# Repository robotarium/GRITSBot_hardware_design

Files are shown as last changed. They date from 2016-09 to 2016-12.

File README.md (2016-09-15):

- [Overview](#overview)
- [Getting Started](#getting-started)
- [Hardware Specifications](#hardware-specifications)
- [Hardware Assembly](#hardware-assembly)

# Overview
This repository contains the GRITSBot's circuit board designs, bill of materials, hardware specifications, and 3D design files. This README file is meant to provide more detailed hardware specifications and a brief tutorial outlining how to get started with the hardware. Specifically, it explains how to program both the motor and the main board.

# Getting Started
The newest version of the GRITSBot features two microcontrollers - an Atmega168/328 (8MHz, 16/32 KB flash, 2 KB RAM) on the motor board and the ESP8266 (80/160 MHz, ~80kB DRAM (Data RAM), ~35kB IRAM (Instruction RAM)) on the main board. Both boards can be programmed through the Arduino IDE but require different toolchains (avr-gcc and Xtensa). Both boards have broken out pins to connect the programmer to. The motor board relies on SPI communication for programming, while the main board's ESP8266 chip has a built-in serial bootloader. Therefore the main board requires only a USB-to-TTL converter to program instead of a programmer for the motor board. Note that for programming, the robot has to be disassembled, i.e. the two boards have to be taken apart (the battery does not have to be disconnected, but it's advisable that the robot's power switch is in the OFF position).

## Motor board programming
The GRITSBot's motor board firmware is available [here](https://github.com/robotarium/GRITSBot_firmware). Before programming the motor board, download all required libraries from that link and copy them to the Arduino IDE's 'libraries' folder.

1. Connect the 6-pin ISP single row programming header (shown in the picture) to the female SPI header pins on the motor board (note that for size reasons, the programming connector on the motor board is a two-row 0.127 inch pitch connector and may require an adapter.)
2. Plug the programmer into the USB port on your host machine (ideally running Linux).
3. Programming the Atmega168/328 chip can be done in a variety of ways 
  * Use a tool called arduino-cmake, a CMake-based toolchain customized for the use of avrdude. The initial setup can be tricky but the tool itself is convenient.
  * Add a board definition to the Arduino IDE's boards.txt file that allows direct programming of the motor board through a programming device in the Arduino IDE.
  * If you have compiled your code already and have a .hex file ready to go, you can use avrdude directly as shown below.

An example of uploading a compiled hex file is shown in the line below, which uploads the "blink.hex" file to the flash memory of an Atmega328 chip through the USB port with the help of an STK500v2 programmer. In the call to _avrdude_ you can see the _-C_ parameter to include its configuration file _avrdude.conf_.
```
avrdude -C avrdude.conf -v -v -v -patmega328 -cstk500v2 -Pusb -Uflash:w:./blink.hex:i -Ulock:w:0x0F:m

```

## Main board programming 
Programming the main board is simpler, since it can be done via a serial adapter. However, attention has to be paid to the operating voltage of the main board, which is 3.3V. The ESP8266 chip is NOT 5V-tolerant and both the supply voltage as well as the serial data signals have to be 3.3V. The following steps assume that your Arduino IDE is set up according to [Sparkfun's tutorial](https://learn.sparkfun.com/tutorials/esp8266-thing-hookup-guide/installing-the-esp8266-arduino-addon). It also assumes that you have downloaded all the GRITSBot's firmware libraries into your Arduino/libraries folder. Then the following steps will program the main board. Note that the GRITSBot's main board firmware is available [here](https://github.com/robotarium/GRITSBot_firmware).

1. Set the "Bootmode" switch on the main board to "Flash" (this ensures that the GPIO0 of the ESP8266 is pulled to logic LOW).
2. Press the push botton on the board to reset the board into programming mode in case the board was powered on before.
3. Select *Generic ESP8266 Module* in the board list of the Arduino IDE (Upload speed can be as high as 921000 Baud, depending on your FTDI adapter).
4. Connect the FTDI serial adapter to the main board and plug the other end into a USB port. Make sure the adapter operates at 3.3V (the broken out pins on the main board contain TX, RX, VCC, and GND).
5. Upload code to the board through the Arduino IDE.

# Hardware Specifications
The robot consists of two individual boards that are stacked through a combination of male and female header pins. 

The main board is the central processing board and responsible for the high-level control of the robot, communication, and power supply. As such, it contains the main microcontroller and a WiFi transceiver. The following list summarizes the main components of the main board.

1. The ESP8266 microcontroller that also hosts the WiFi hardware and runs the WiFi stack in software. The ESP8266 chip contains an SPI-controlled EEPROM chip that enables the chip to be wirelessly reprogrammed. The newest version of the GRITSBot contains the ESP8266 12-E with 4 MB (32 MBit) of flash memory, which allows firmware upgrades over-the-air ([see Adafruit](https://www.adafruit.com/products/2491)).
2. MCP73831 LiPo battery charging chip
3. AP2112K-3.3V 3.3V voltage regulator (capable of providing 600 mA of current, which is necessary since the ESP8266 can have peak current consumptions of 300 mA)
4. MCP1640 step-up converter for powering the motors on the motor board (capable of providing 150 mA)
5. INA219 I2C-enabled current and voltage sensor 
6. ATECC108 encryption and authentication chip

The following two images show the top and the bottom layer of the main board PCV
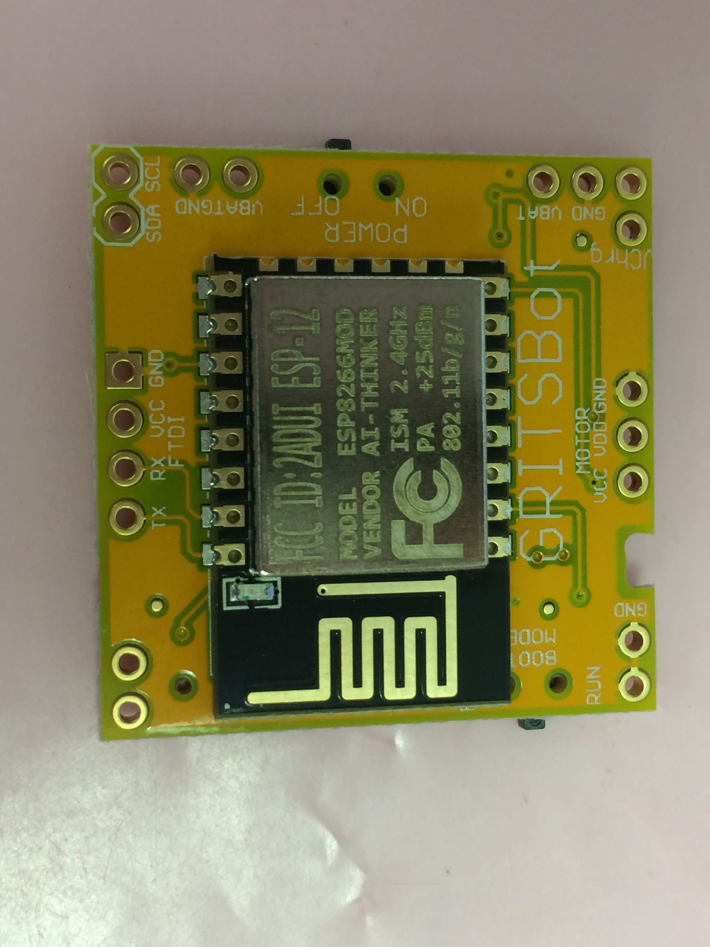
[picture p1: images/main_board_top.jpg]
Top layer of the main board

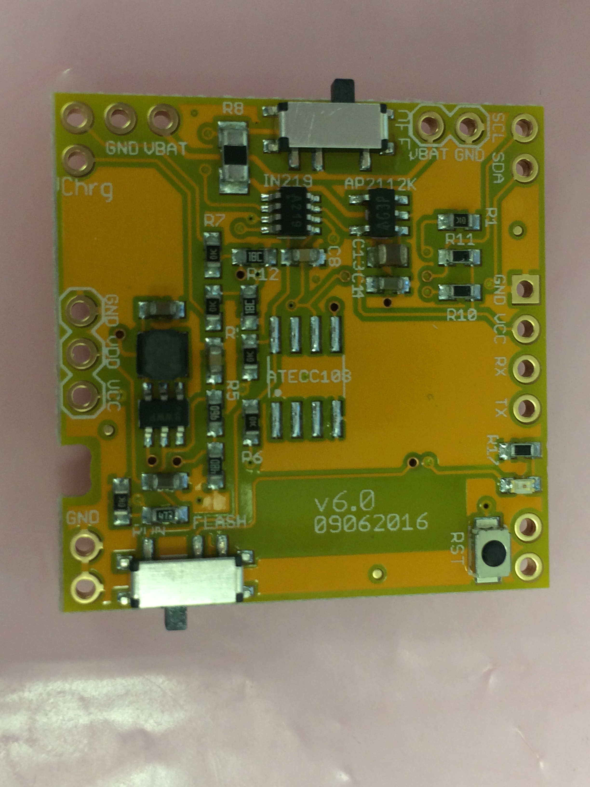
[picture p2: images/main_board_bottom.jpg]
Bottom layer of the main board


The motor board contains all components related to locomotion including a microcontroller to control the stepper motors. An additional EEPROM chip allows storing calibration parameters and equips each motor board with a unique ID. Additionally, the motor board contains downward-facing infrared sensors for line-following applications as well as introspective sensors to measure the state of the motor board (e.g. currents and temperatures).

1. One Atmega168/328 microcontroller (the motor board firmware requires over 9 KB which excludes the Atmega88 chip)
2. Two LB1836M motor drivers
3. Two miniature stepper motors
4. One 24AA025UIDT-I/OT 2KBIT I2C EEPROM chip providing a unique ID to each motor board.
5. Two QRE1113 downward-facing infrared line sensors 
6. Two STLM20 temperature sensors measuring motor temperatures
7. Two ZXCT1009 current sensors measuring motor currents
6. Reverse polarity circuitry protecting charger input pins
7. Two LEDs for visual output and debugging

The following two images show the top and the bottom layer of the main board PCV
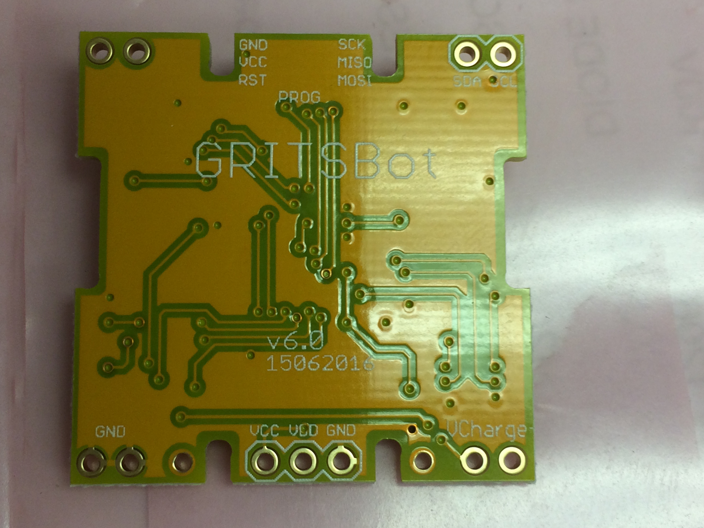
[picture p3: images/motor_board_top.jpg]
Top layer of the motor board

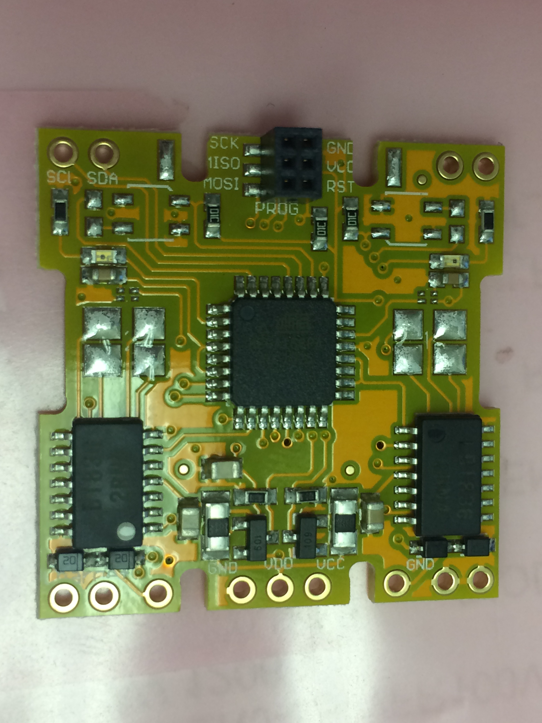
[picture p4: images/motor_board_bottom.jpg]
Bottom layer of the motor board


# Hardware Assembly
Assembly of the GRITSBot is fairly simple in the sense that few components have to be added once all the circuit boards have been populated with SMD components (services such as Seeedstudio or Circuithub can manufacture and populate the boards for a reasonable price). Manufacturers can also populate the throughhole components (i.e. the male and female header pins) but so far we have done that manually. The main and motor boards have matching male/female headers that can only be stacked in one way. The __assembly sequence__ contains the following steps. 

## Main board assembly
1. Solder a female Losi Micro Walkera 2-Pin Connector plug to the main board's battery pins (i.e. VBAT and neighboring GND pin)
2. Solder a 4-pin male programming header pin to the top of the main board (i.e. the pins TX, RX, Vcc, GND). Note that the top side of the board is the one with the ESP8266 12-E part.
3. Solder four 2-pin male header pins to all four corners on the bottom of the main board. In the schematic and board files, these pins are labeled JP\_RST, JP\_I2C, JP\_GND, and JP\_VCHRG\_IN.
4. Solder a 3-pin female header pin to the power pins in the center of the bottom of the board (labeled "MOTOR", containing the pins Vcc, Vdd, and GND).

## Motor board assembly
The motor board assembly contains a few more steps since the motors have to be soldered on besides the male and female header pins. In addition, the Qi charging coil and receiver circuitry have to be attached to the board. 

### Prepare and mount the motors and wheels
1. Tap the wheels with an M1.7 thread plug.
2. Screw one wheel onto each motor.
3. Solder both motors onto the motor board (a video showing this procedure will follow soon)

### Solder on the connectors
1. Solder four 2-pin female header pins to all four corners on the top of the motor board. In the schematic and board files, these pins are labeled JP\_RST, JP\_I2C, JP\_GND, and JP\_VCHRG.
2. Solder a 3-pin male header pin to the power pins in the center of the top of the motor board (containing the pins Vcc, Vdd, and GND).

### Prepare the Qi receiver parts
1. Disassemble the Qi receiver pad (see bill of materials specifying which receiver pad to purchase).
2. Desolder the USB connector and the coil from the receiver assembly.

### Attach the Qi receiver parts
1. Glue or tape the Qi receiver coil to the 3D part [Charging Coil Base](https://github.com/robotarium/GRITSBot_hardware_design/blob/master/3d_model/Charging_frame_base.stp).
2. Tape the Qi receiver circuitry to the top of the motor board.
3. Solder a wire to each output pin of the receiver circuitry (those pins should be labeled '+' and '-' or '5V' and 'Gnd').
4. Solder the other end of these wires to the following motor board pins: JP\_CHRG\_L and JP\_CHRG\_R
5. Cut the receiver coil wires to the right length and solder them to the input pins of the receiver circuitry. Those pins may not be labeled on the receiver circuitry, but attach them to the same pins that you desoldered them before.

## Robot assembly
2. Sandwich the battery between the motor and the main board and wrap the battery cable around the robot.
3. Stack the motor and the main board keeping the battery in place.
5. Connect battery to the main board.

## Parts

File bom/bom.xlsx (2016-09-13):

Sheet: Main Board
Part/Designator | Manufacture Part Number/Seeed SKU | Quantity | Info | DigiKey part # | Ebay Link
AP2112K | AP2112K-3.3TRG1 | 1 | voltage regulator | AP2112K-3.3TRG1DICT-ND
BTN_RST | PTS820 J15M SMTR LFS | 1 | reset button | CKN10506CT-ND
C1 | CC0805ZKY5V6BB106 | 1 | 10uF | 311-1355-1-ND
C2, C8 | CC0603KRX7R7BB104 | 2 | 0.1uF | 311-1088-1-ND
C3, C4 | CL10A475KO8NNNC | 2 | 4.7uF | 1276-1784-1-ND
C5 | C3216JB1E336M160AC | 1 | 30uF | 445-11710-1-ND
C13 | CC0603ZRY5V7BB105 | 1 | 1.0uF | 311-1372-1-ND
C14 | CC0603KRX5R6BB225 | 1 | 2.2uF | 311-1451-1-ND
ESP8266 | 1528-1438-ND | 1 | Digikey (Adafruit: #2491) | 1528-1438-ND
INA219 | INA219AIDCNR | 1 | current monitor chip | 296-23770-1-ND
JP_FTDI | M20-9990446 | 1 | 4 pin, 0.254mm pitch, male header pin | 952-2266-ND
JP_GND, JP_I2C, JP_RST, JP_VCHRG_IN | M20-9990246 | 4 | 2 pin, 0.254mm pitch male header pin | 952-2262-ND
JP_MOTOR | PPPC031LFBN-RC | 1 | 3 pin, 0.254mm pitch female header pin | S7036-ND
JP_LIPO | Losi Micro Walkera 2-Pin Connector plug | 1 |  |  | e.g. http://www.ebay.com/itm/Losi-Micro-Walkera-2-Pin-Connector-plug-Male-Female-Crimps-x-50-Sets-/171361716288
L1 | NR3015T4R7M | 1 | 4.7uH | 587-1649-1-ND
LED_CHRG | 5988020107F | 1 | red | 350-2030-1-ND
LED_USER | 5988060107F | 1 | green | 350-2034-1-ND
MCP1640 | MCP1640BT-I/CHY | 1 | Boost converter | MCP1640BT-I/CHYCT-ND
MCP73831 | MCP73831T-2ACI/OT | 1 | LiPo charging chip | MCP73831T-2ACI/OTCT-ND
POWER_SWITCH, RUNMODE_SWITCH | PCM12SMTR | 2 | switches | 401-2016-1-ND
R1, R4, R5, R6, R7, R13 | RC0603FR-0710KL | 6 | 10k | 311-10.0KHRCT-ND
R2 | RC0603FR-07976KL | 1 | 976k | 311-976KHRCT-ND
R3 | RC0603FR-07309KL | 1 | 309k | 311-309KHRCT-ND
R8 | ERJ-8BWFR100V | 1 | 0.1 | P.10AUCT-ND
R9, R12 | RC0603FR-0715KL | 2 | 15k | 311-15.0KHRCT-ND
R10, R11, R16 | RC0603FR-072KL | 3 | 2.0k | 311-2.00KHRCT-ND
R15, R17 | RC0603FR-071KL | 2 | 1.0k | 311-1.00KHRCT-ND
R14 | RC0603FR-0749K9L | 1 | 50k | 311-49.9KHRCT-ND
U1 | ATECC108A-SSHCZ-B | 1 | encryption chip | ATECC108A-SSHCZ-B-ND

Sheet: Motor Board
Part/Designator | Manufacture Part Number | Quantity | Info | DigiKey part # | Ebay Link
ATMEGA168P | ATMEGA168PA-AU | 1 | Atmel 32-pin 8-bit micro, 16k flash. | ATMEGA168PA-AU-ND
C1, C2, C9 | CC0805ZKY5V6BB106 | 3 | 10 uF | 311-1355-1-ND
C3, C4 | CC0603KRX7R7BB104 | 2 | 0.1uF | 311-1088-1-ND
CUR_LEFT, CUR_RIGHT | ZXCT1009FTA | 2 | current monitor chip | ZXCT1009FCT-ND
D1, D2, D3, D4 | BAT20JFILM | 4 | BAT20J | 497-3381-1-ND
JP_I2C, JP_GND, JP_RST, JP_VCHRG | PPPC021LFBN-RC | 4 | 2 pin, 0.254mm pitch female header pin | S7035-ND
JP_POWER | M20-9990346 | 1 | 3 pin, 0.254mm pitch male header pin | 952-2264-ND
JP_PROG | 20021321-00006C4LF | 1 | 6 pin, 0.127mm pitch female header pin | 609-3704-1-ND
LED_LEFT, LED_RIGHT | 5988060107F | 2 | green LED | 350-2034-1-ND
LINE_SENSE_1, LINE_SENSE_2 | QRE1113GR | 2 | QRE1113 | QRE1113GRCT-ND
M1, M2 | www.ebay.com | 2 | miniature stepper motor |  | http://www.ebay.com/itm/10PC-2-Phase-4-Wire-micro-stepper-motor-stepping-motor-Dia-6mm-With-small-screw/251743546959
MEM | 24AA025UIDT-I/OT | 1 | memory chip | 24AA025UIDT-I/OTCT-ND
MOTOR_CTRL_1, MOTOR_CTRL_2 | LB1836M-TLM-E | 2 | LB1836M | 869-1218-1-ND
R1, R3 | RC0603FR-071KL | 2 | 1k | 311-1.00KHRCT-ND
R2, R6, R8, R10, R11 | RC0603FR-0710KL | 5 | 10k | 311-10.0KHRCT-ND
R5, R7 | RC0603FR-07100RL | 2 | 100 | 311-100HRCT-ND
R4, R9 | ERJ-8BWFR100V | 2 | 0.1 | P.10AUCT-ND
TEMP_LEFT, TEMP_RIGHT | STLM20DD9F | 2 | temperature sensor | 497-5814-1-ND

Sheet: Additional Components
Part/Designator | Manufacture Part Number/Seeed SKU | Quantity | Info | Link
Wheels | RB-Sbo-09 | 2 | Miniature Rubber Wheel (by Solarbotics) | http://www.robotshop.com/en/solarbotics-rw-miniature-rubber-wheels.html
Motors | Ebay or AliExpress | 2 | 2-phase 4-wire stepper motor 6mm Canon Micro Stepper Motor diameter: 6 MM Height: 7 MM (excluding front and rear bearing sleeve) Output shaft: 1.5 MM (with a small Division rod) Output shaft length: 8.5 MM | http://www.ebay.com/itm/10pcs-With-a-small-the-screw-2-phase-4-wire-stepper-motor-6mm-Canon-Micro-/161032829736 Or http://www.aliexpress.com/item/Wholesale-diy-20-PCS-4-Wire-2-Phase-Miniature-stepper-motor-With-a-small-screw-D6mm/1604748688.html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
Battery | LXWLT9 | 1 | Great Planes LiPo 1S 3.7V 400mAh Battery Novus CX/FP/CP | http://www3.towerhobbies.com/cgi-bin/wti0001p?&I=LXWLT9&P=7
3D-printed parts | PLA or ABS filament | 1 | ~50g of material | http://www.makergear.com/collections/filament/products/pla?variant=21668447044
Charging coil and transmitter | Amazon | 1 | KINGMAS® Universal Qi Wireless Charging Receiver Card with Charger Pad | https://www.amazon.com/dp/B01193R0SQ?colid=3DBYL08Q1XT72&coliid=I3TN1IC5CG2VQ7

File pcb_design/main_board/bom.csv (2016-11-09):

Part/Designator | Manufacture Part Number/Seeed SKU | Quantity | Info | DigiKey part # | Ebay Link
AP2112K | AP2112K-3.3TRG1 | 1 | voltage regulator | AP2112K-3.3TRG1DICT-ND
BTN_RST | PTS820 J15M SMTR LFS | 1 | reset button | CKN10506CT-ND
C1, C15 | CC0603MRX5R6BB106 | 1 | 10uF | 311-1817-1-ND
C2, C8, C9, C10, C11 | CC0603KRX7R7BB104 | 2 | 0.1uF | 311-1088-1-ND
C3, C4 | CL10A475KO8NNNC | 2 | 4.7uF | 1276-1784-1-ND
C5 | C3216JB1E336M160AC | 1 | 30uF | 445-11710-1-ND
C12 | CC0603JRX7R9BB103 | 1 | 10nF | 311-1778-1-ND
C13 | CC0603ZRY5V7BB105 | 1 | 1.0uF | 311-1372-1-ND
C14 | CC0603KRX5R6BB225 | 1 | 2.2uF | 311-1451-1-ND
D1, D2 | 1528-1104-ND | 2 | WS2812 RGB LED | 1528-1104-ND
ESP8266 | 1528-1438-ND | 1 | Digikey (Adafruit: #2491) | 1528-1438-ND
INA219 | INA219AIDCNR | 1 | current monitor chip | 296-23770-1-ND
JP_FTDI | M20-9990446 | 1 | 4 pin, 0.254mm pitch, male header pin | 952-2266-ND
JP_GND, JP_I2C, JP_RST, JP_VCHRG_IN | M20-9990246 | 4 | 2 pin, 0.254mm pitch male header pin | 952-2262-ND
JP_MOTOR | PPPC031LFBN-RC | 1 | 3 pin, 0.254mm pitch female header pin | S7036-ND
JP_LIPO | Losi Micro Walkera 2-Pin Connector plug | 1 |  |  | e.g. http://www.ebay.com/itm/Losi-Micro-Walkera-2-Pin-Connector-plug-Male-Female-Crimps-x-50-Sets-/171361716288
L1 | NR3015T4R7M | 1 | 4.7uH | 587-1649-1-ND
LED_CHRG | 5988020107F | 1 | red | 350-2030-1-ND
LED_USER | 5988060107F | 1 | green | 350-2034-1-ND
MCP1640 | MCP1640BT-I/CHY | 1 | Boost converter | MCP1640BT-I/CHYCT-ND
MCP73831 | MCP73831T-2ACI/OT | 1 | LiPo charging chip | MCP73831T-2ACI/OTCT-ND
POWER_SWITCH, RUNMODE_SWITCH | PCM12SMTR | 2 | switches | 401-2016-1-ND
R1, R4, R5, R6, R13 | RC0603FR-0710KL | 6 | 10k | 311-10.0KHRCT-ND
R2 | RC0603FR-07976KL | 1 | 976k | 311-976KHRCT-ND
R3 | RC0603FR-07309KL | 1 | 309k | 311-309KHRCT-ND
R8 | ERJ-8BWFR100V | 1 | 0.1 | P.10AUCT-ND
R9 | RC0603FR-0715KL | 2 | 15k | 311-15.0KHRCT-ND
R10, R11 | RC0603FR-074K7L | 2 | 4.7k | 311-4.70KHRCT-ND
R16 | RC0603FR-072KL | 1 | 2.0k | 311-2.00KHRCT-ND
R15, R17 | RC0603FR-071KL | 2 | 1.0k | 311-1.00KHRCT-ND
R18 | RC0603FR-074K99L | 1 | 4.99k | 311-4.99KHRCT-ND
R14 | RC0603FR-0749K9L | 1 | 50k | 311-49.9KHRCT-ND
R19 | 742C083103JP | 1 | 10k resistor array | 742C083103JPCT-ND
U1 | ATECC108A-SSHCZ-B | 1 | encryption chip | ATECC108A-SSHCZ-B-ND
U2 | TMP102AIDRLR | 1 | TMP102 temperature sensor | 296-26834-1-ND
U3 | LSM9DS1TR | 1 | LSM9DS1 IMU | 497-14946-1-ND

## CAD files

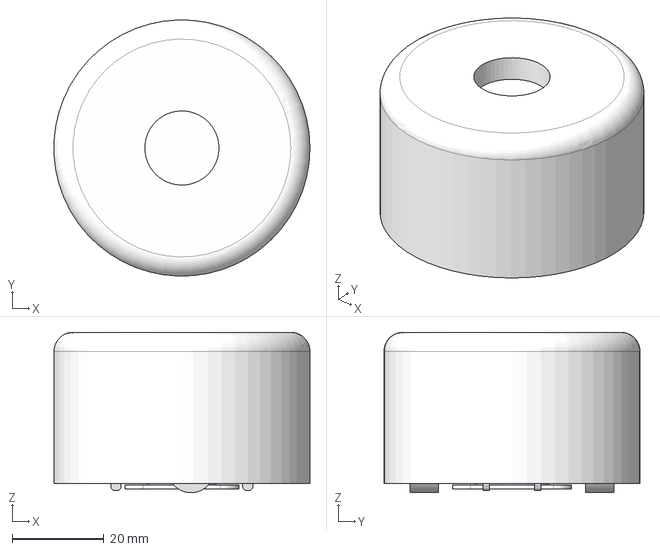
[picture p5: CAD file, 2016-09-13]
3d_model/Main.stp
55.8 x 55.9 x 35.0 mm

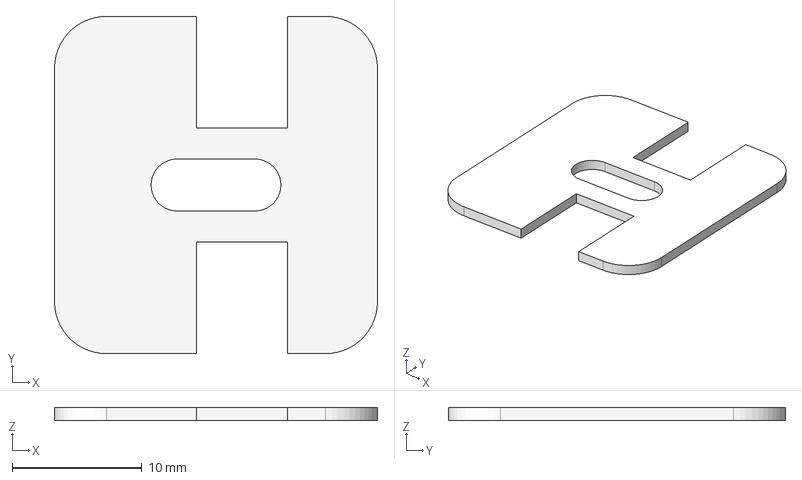
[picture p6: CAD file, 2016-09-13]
3d_model/Charging_frame_base.stp
24.9 x 26.0 x 1.00 mm

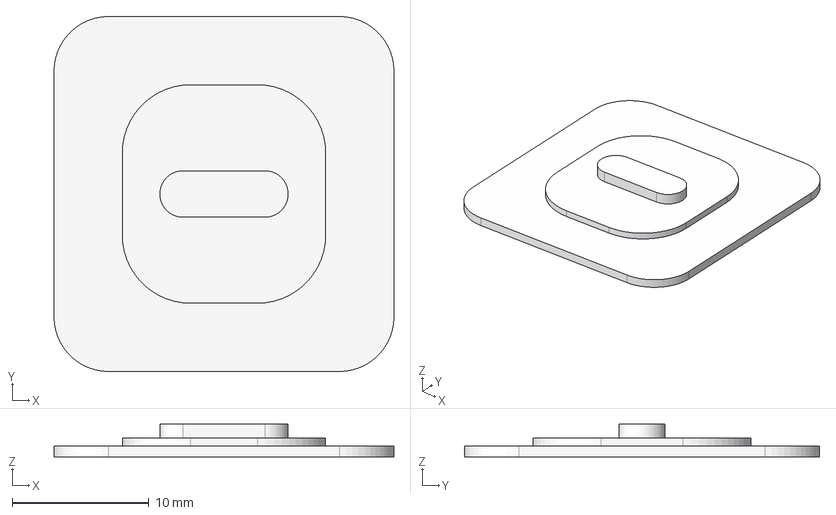
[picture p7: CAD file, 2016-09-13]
3d_model/Charging_frame_cap.stp
24.9 x 26.0 x 2.40 mm

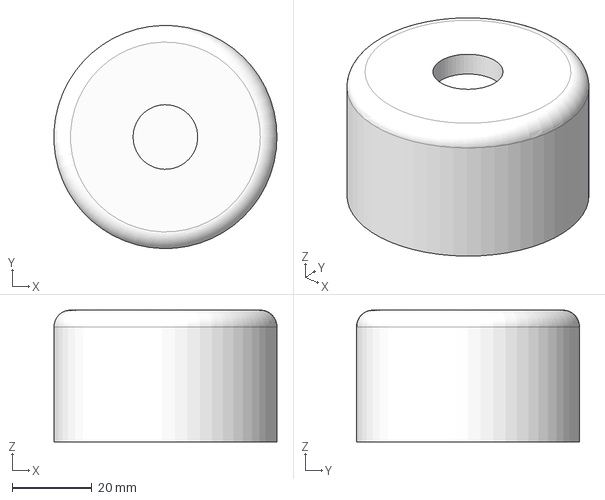
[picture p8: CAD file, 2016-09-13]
3d_model/Shell.stp
55.8 x 55.9 x 33.0 mm

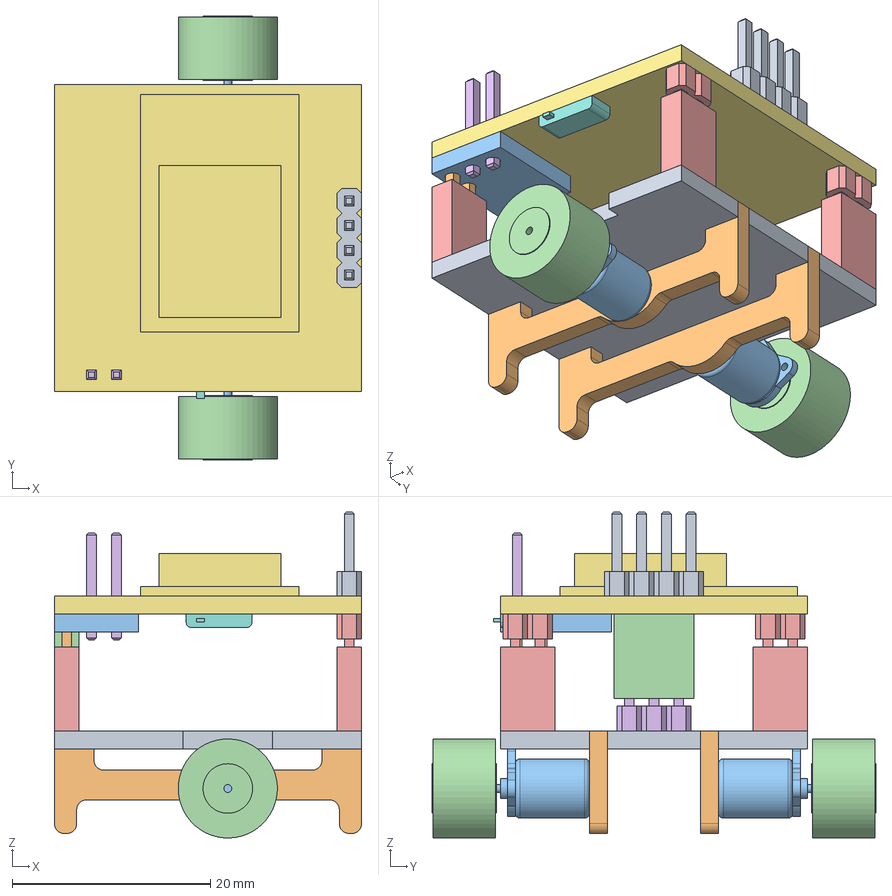
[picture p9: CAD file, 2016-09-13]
3d_model/Frame.stp
31.0 x 44.8 x 32.9 mm

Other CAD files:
3d_model/Frame.ipt
3d_model/Main.ipt

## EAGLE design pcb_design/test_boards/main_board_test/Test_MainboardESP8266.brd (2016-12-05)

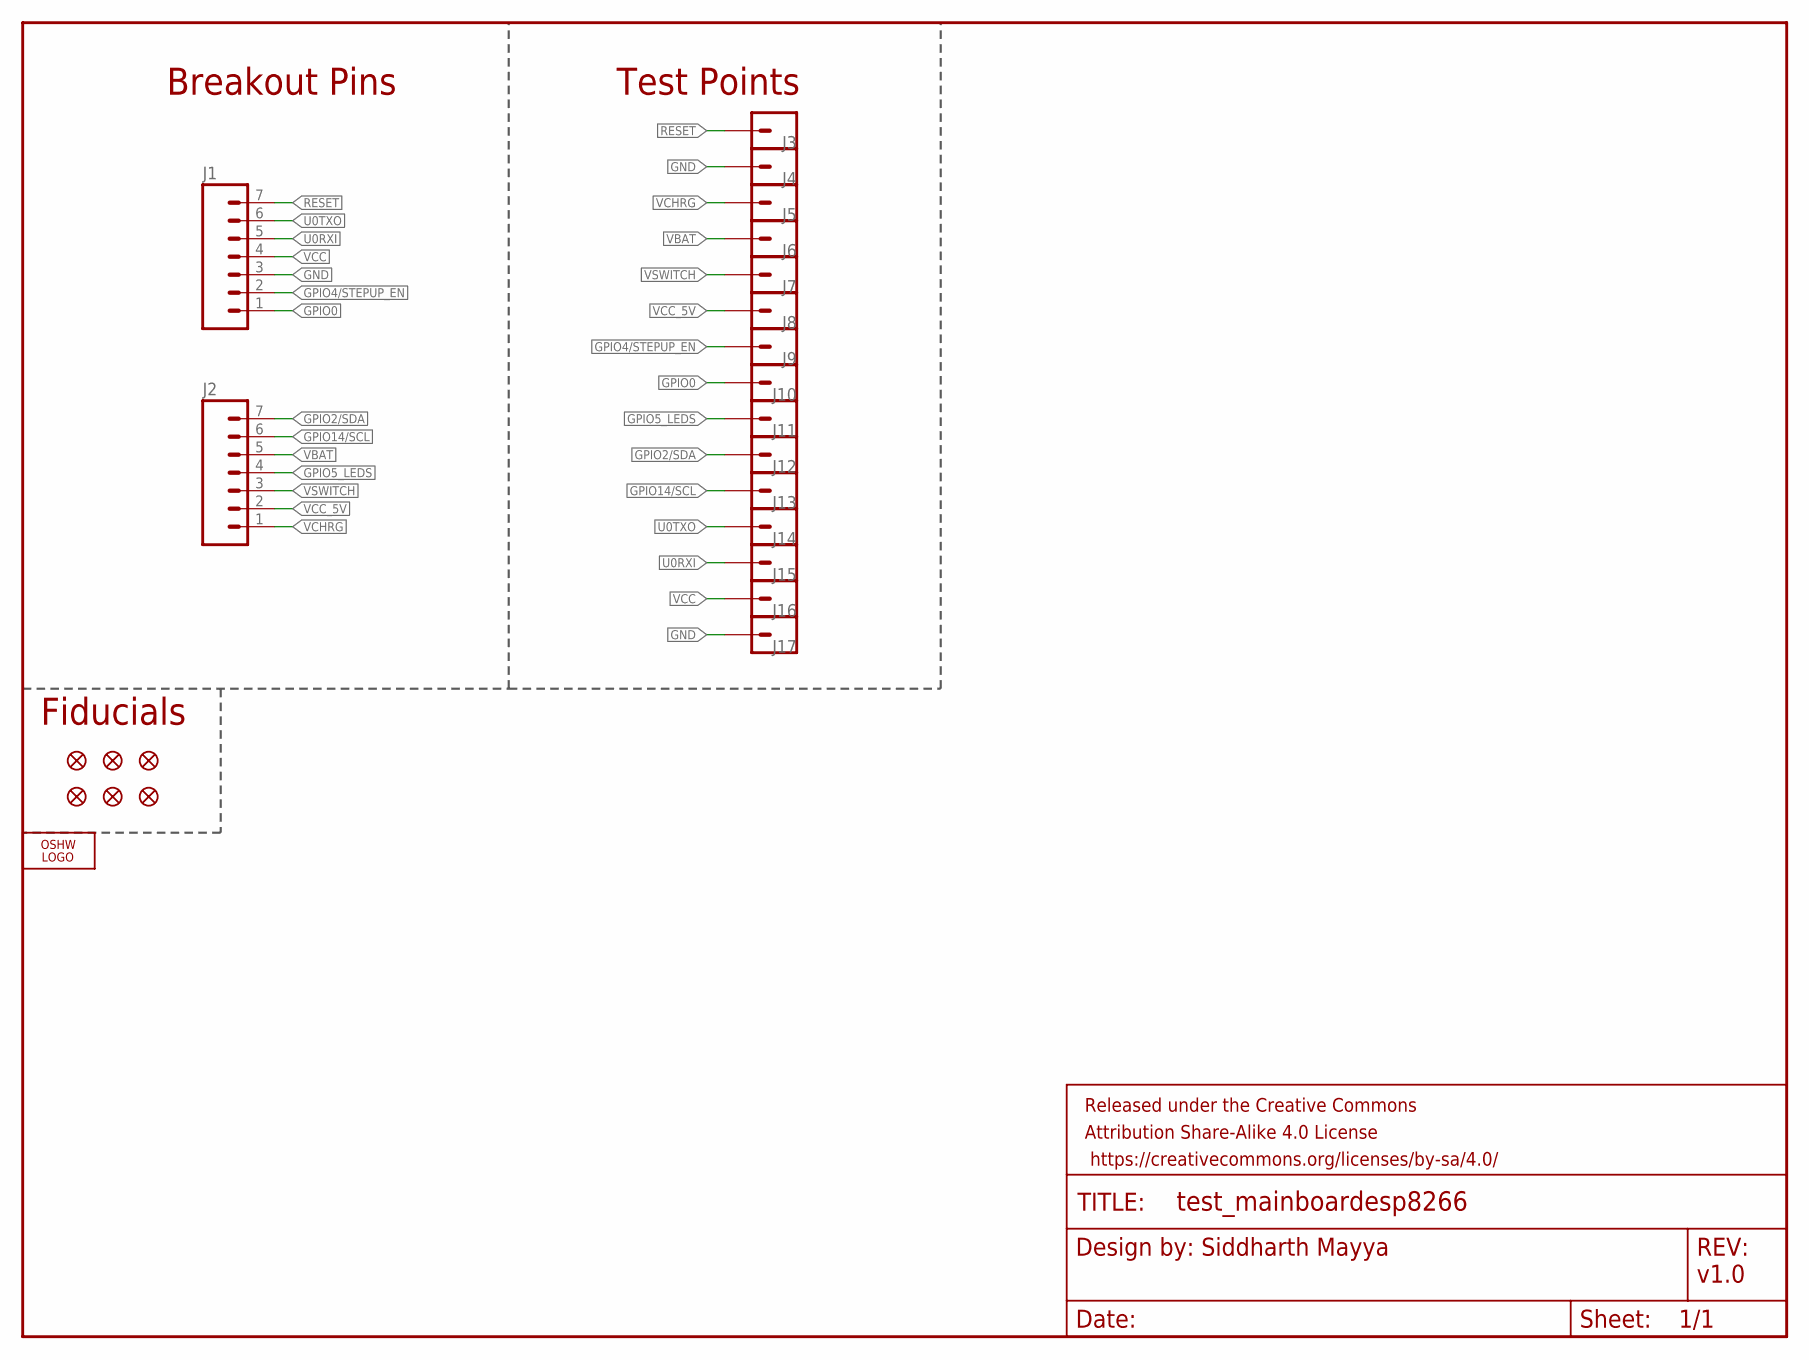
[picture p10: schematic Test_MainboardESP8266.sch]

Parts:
FD1, FD2, FD3, FD4, FD5, FD6: FIDUCIAL1X2; FIDUCIAL-1X2
FRAME1: FRAME-LETTER; CREATIVE_COMMONS
J1, J2: M07; 1X07
J3, J4, J5, J6, J7, J8, J9, J10, J11, J12, J13, J14, J15, J16, J17: M01PTH; 1X01
LOGO1: OSHW_LOGO_FILLX0100-NT; OSHW_FILLX100_NOTEXT

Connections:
GND: J1.3, J4.1, J17.1
GPIO0: J1.1, J10.1
GPIO2/SDA: J2.7, J12.1
GPIO4/STEPUP_EN: J1.2, J9.1
GPIO5_LEDS: J2.4, J11.1
GPIO14/SCL: J2.6, J13.1
RESET: J1.7, J3.1
U0RXI: J1.5, J15.1
U0TXO: J1.6, J14.1
VBAT: J2.5, J6.1
VCC: J1.4, J16.1
VCC_5V: J2.2, J8.1
VCHRG: J2.1, J5.1
VSWITCH: J2.3, J7.1

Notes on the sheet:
v1.0
Test Points
Breakout Pins
Fiducials

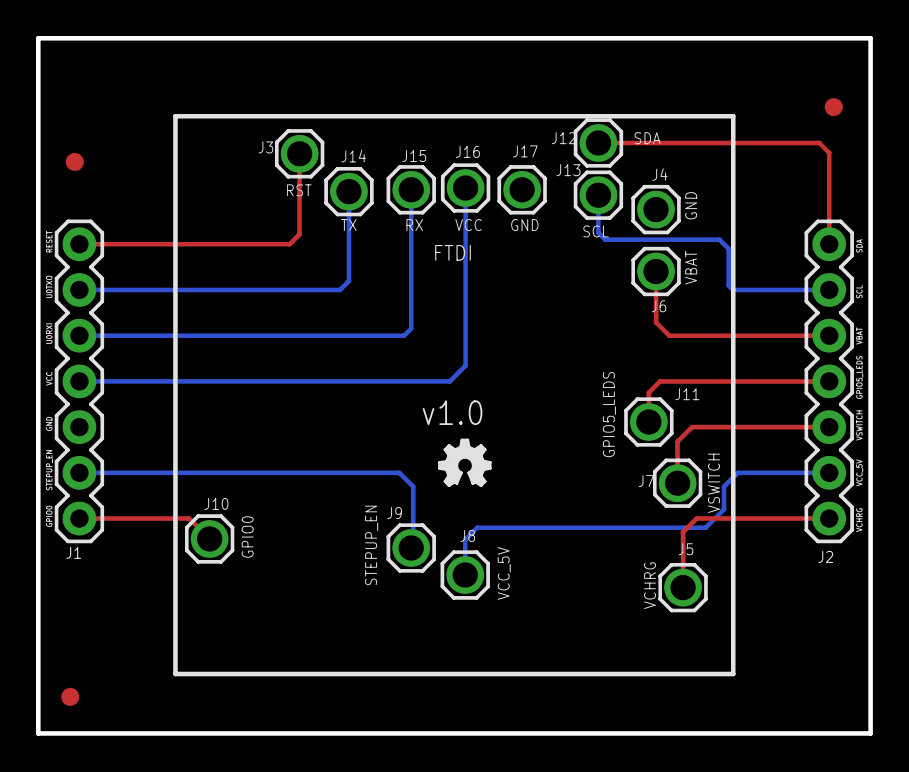
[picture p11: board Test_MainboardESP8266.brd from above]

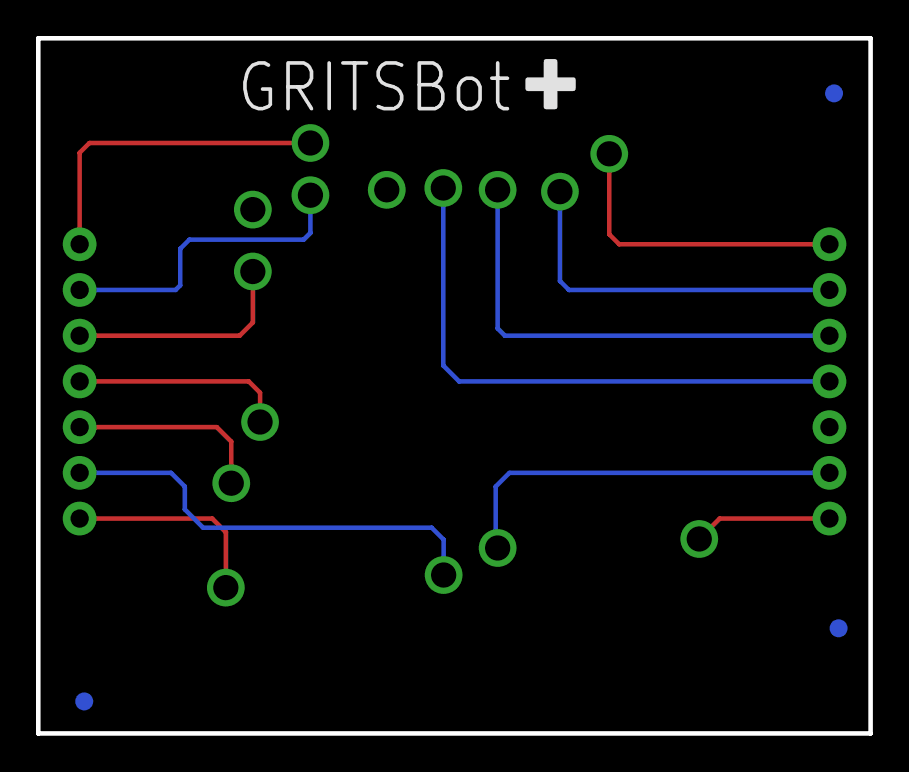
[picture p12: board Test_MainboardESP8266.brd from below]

Board: 2 copper layers, 46.2 x 38.6 mm, 25 parts (3 on the bottom side), 14 nets.

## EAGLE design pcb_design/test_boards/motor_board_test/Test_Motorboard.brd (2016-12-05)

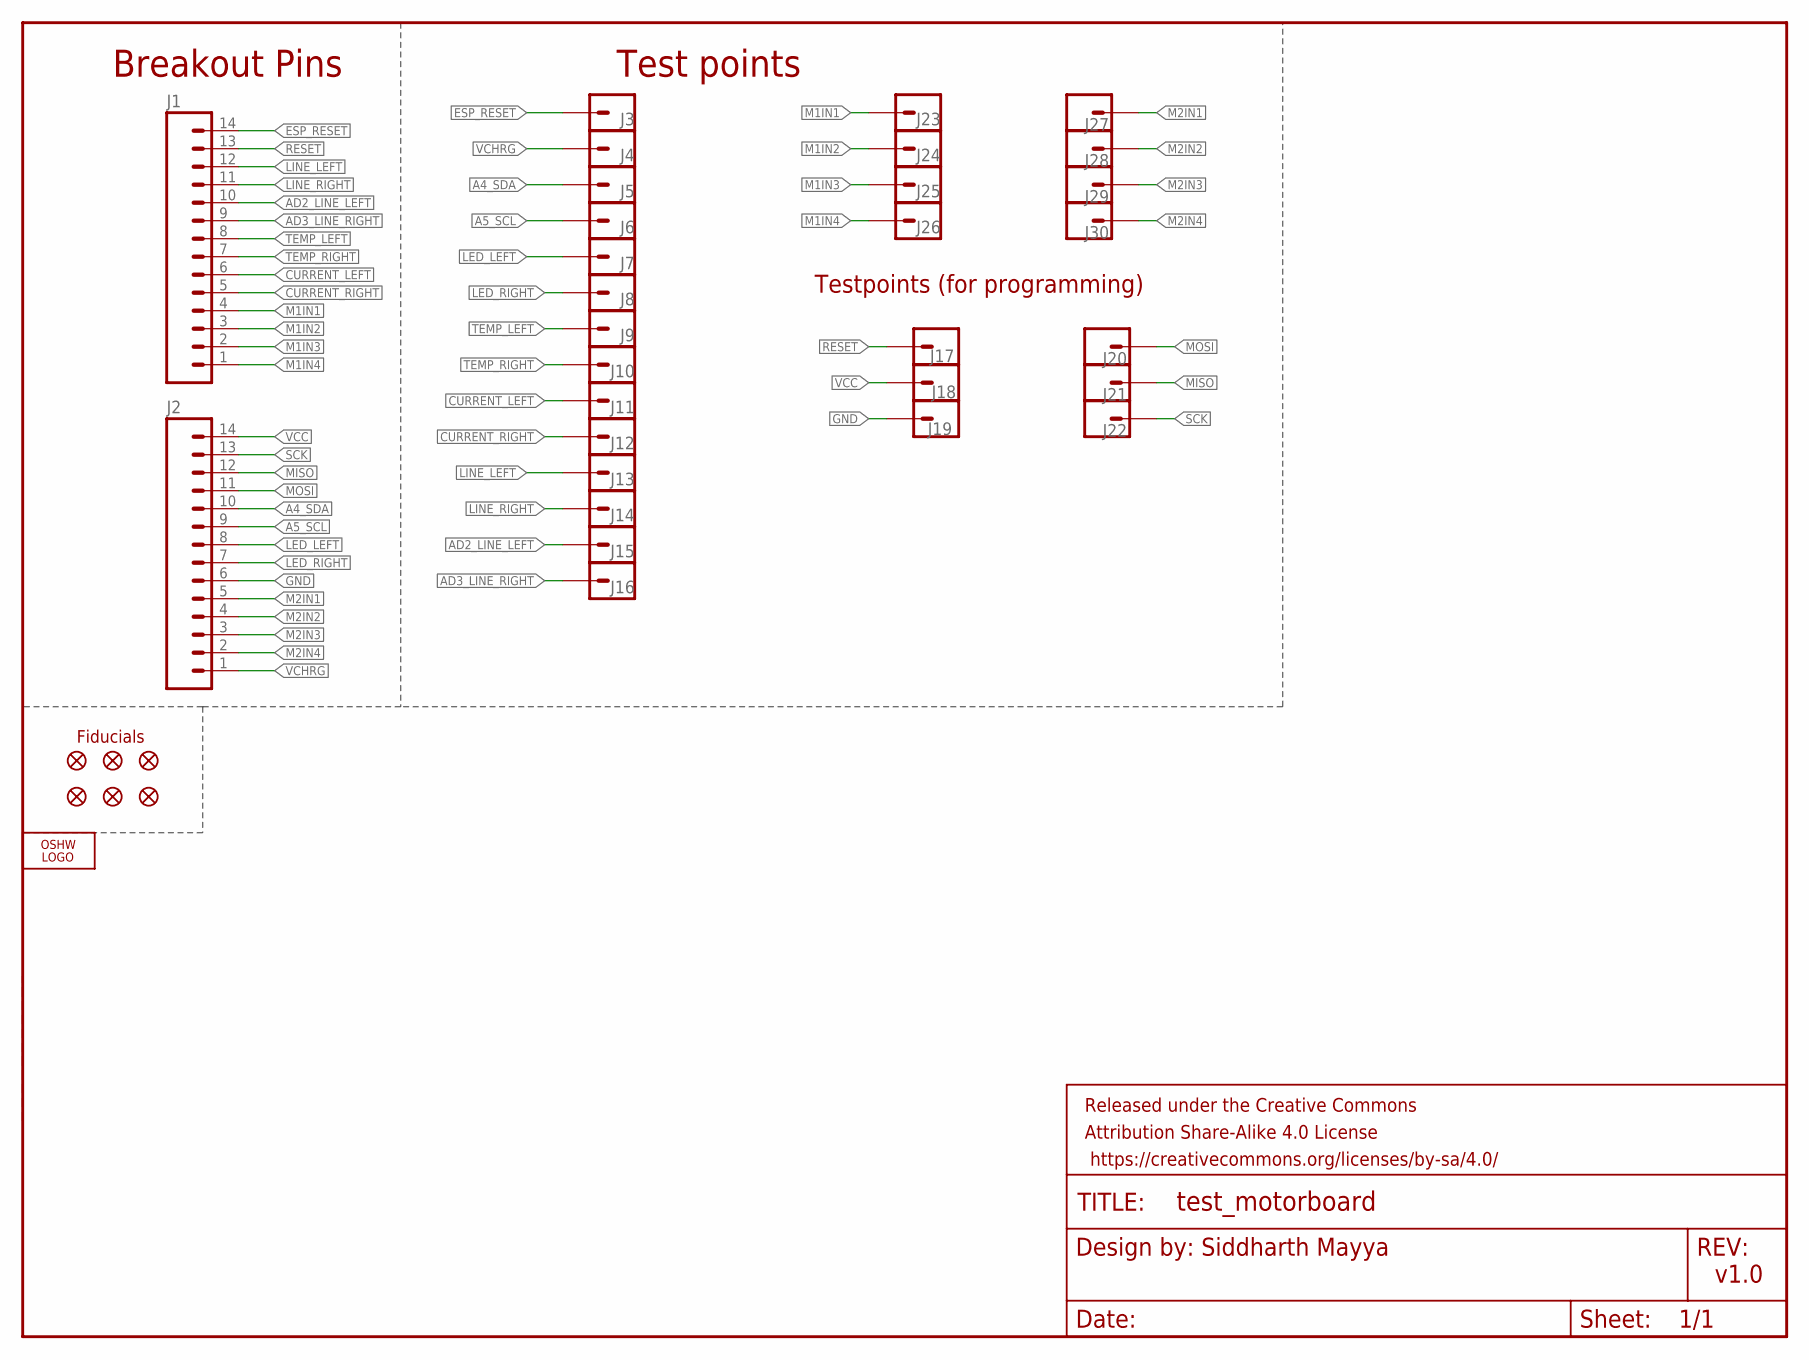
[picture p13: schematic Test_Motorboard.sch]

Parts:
FD1, FD2, FD3, FD4, FD5, FD6: FIDUCIAL1X2; FIDUCIAL-1X2
FRAME1: FRAME-LETTER; CREATIVE_COMMONS
J1, J2: M14; 1X14
J3, J4, J5, J6, J7, J8, J9, J10, J11, J12, J13, J14, J15, J16, J17, J18, J19, J20, J21, J22, J23, J24, J25, J26, J27, J28, J29, J30: M01PTH; 1X01
LOGO1: OSHW_LOGO_FILLX0100-NT; OSHW_FILLX100_NOTEXT

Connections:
A4_SDA: J2.10, J5.1
A5_SCL: J2.9, J6.1
AD2_LINE_LEFT: J1.10, J15.1
AD3_LINE_RIGHT: J1.9, J16.1
CURRENT_LEFT: J1.6, J11.1
CURRENT_RIGHT: J1.5, J12.1
ESP_RESET: J1.14, J3.1
GND: J2.6, J19.1
LED_LEFT: J2.8, J7.1
LED_RIGHT: J2.7, J8.1
LINE_LEFT: J1.12, J13.1
LINE_RIGHT: J1.11, J14.1
M1IN1: J1.4, J23.1
M1IN2: J1.3, J24.1
M1IN3: J1.2, J25.1
M1IN4: J1.1, J26.1
M2IN1: J2.5, J27.1
M2IN2: J2.4, J28.1
M2IN3: J2.3, J29.1
M2IN4: J2.2, J30.1
MISO: J2.12, J21.1
MOSI: J2.11, J20.1
RESET: J1.13, J17.1
SCK: J2.13, J22.1
TEMP_LEFT: J1.8, J9.1
TEMP_RIGHT: J1.7, J10.1
VCC: J2.14, J18.1
VCHRG: J2.1, J4.1

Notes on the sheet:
Breakout Pins
Testpoints (for programming)
Test points
Fiducials
v1.0

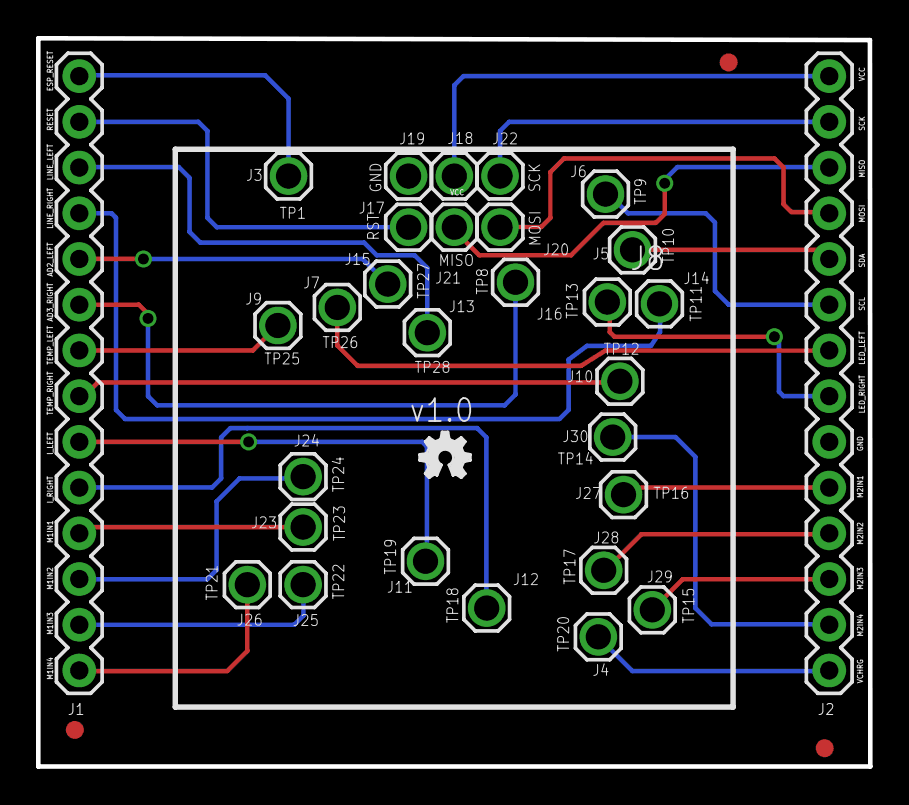
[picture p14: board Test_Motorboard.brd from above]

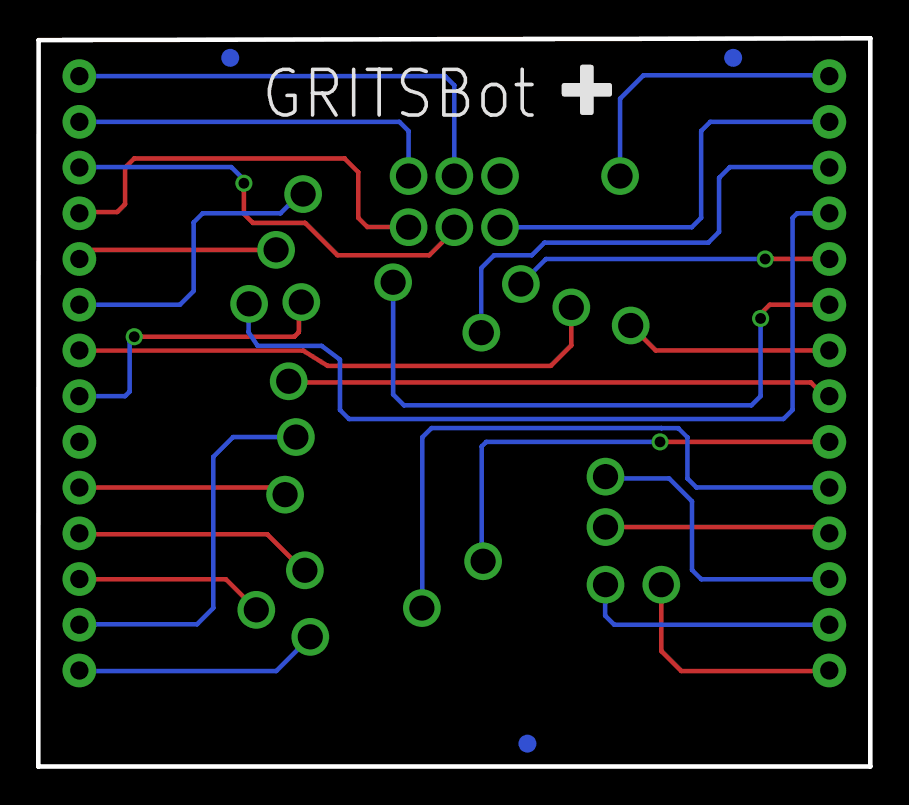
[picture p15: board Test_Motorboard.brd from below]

Board: 2 copper layers, 46.2 x 40.5 mm, 39 parts (3 on the bottom side), 28 nets.

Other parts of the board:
FRAME3: FRAME-LETTER; CREATIVE_COMMONS

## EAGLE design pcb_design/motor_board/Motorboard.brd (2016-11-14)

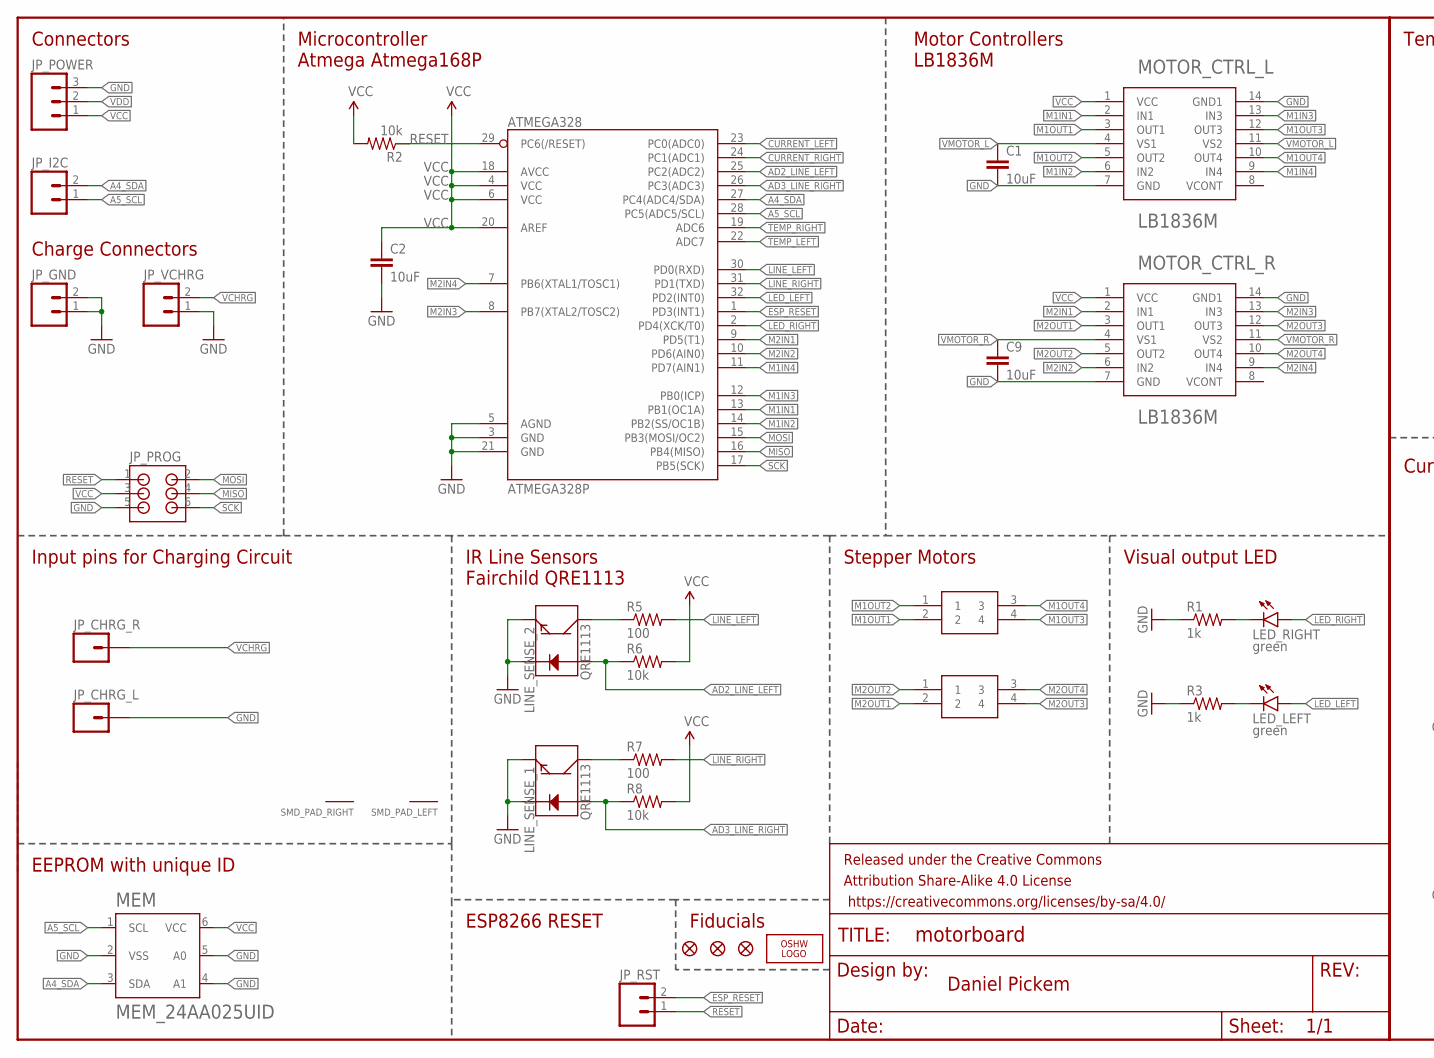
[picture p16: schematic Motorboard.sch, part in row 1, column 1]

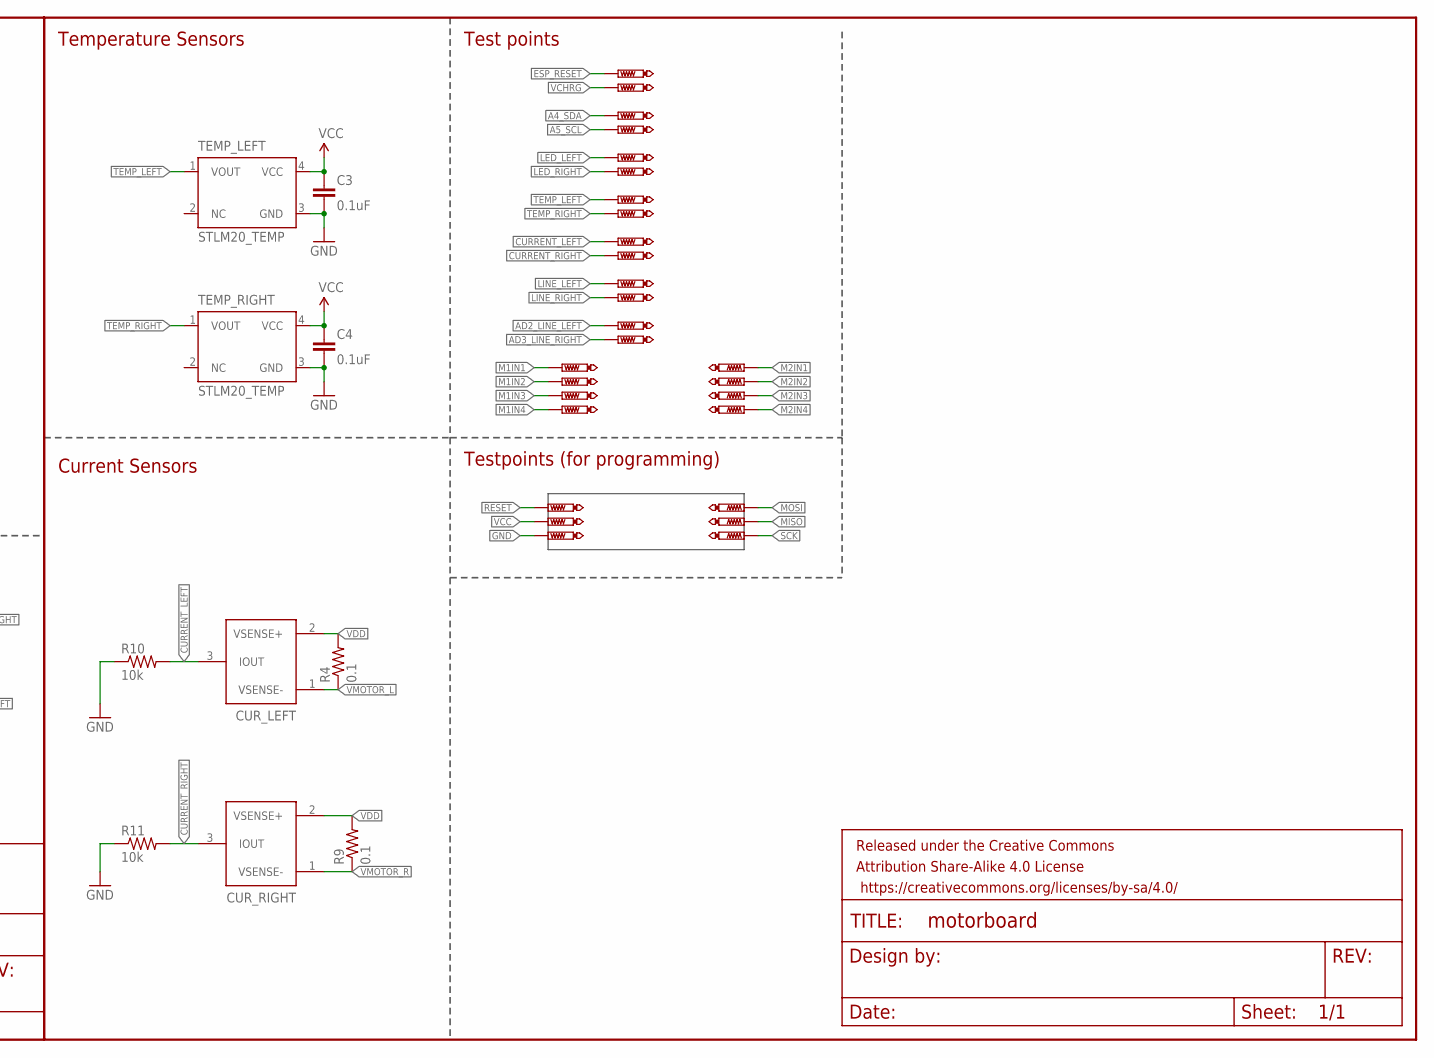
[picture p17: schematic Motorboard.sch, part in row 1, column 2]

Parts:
ATMEGA328P: ATMEGA328; TQFP32-08
C1, C2, C9: 10uF; 0805
C3, C4: 0.1uF; 0603-CAP
CUR_LEFT: ZXCT1009_CURRENT; SOT23-3
CUR_RIGHT: ZXCT1009_CURRENT; SOT23-3
FRAME1, FRAME2: FRAME-LETTER; CREATIVE_COMMONS
JP3, JP4, JP5: FIDUCIAL1X2.5; FIDUCIAL-1X2.5
JP_CHRG_L: M01NOSILK-KIT; 1X01NS-KIT
JP_CHRG_R: M01NOSILK-KIT; 1X01NS-KIT
JP_GND: M021X02_NO_SILK; 1X02_NO_SILK
JP_I2C: M02PTH; 1X02
JP_POWER: supply; 1X03
JP_PROG: 3X2_SMD_HEADER
JP_RST: M021X02_NO_SILK; 1X02_NO_SILK
JP_VCHRG: M021X02_NO_SILK; 1X02_NO_SILK
LED_LEFT: green; LED-0603
LED_RIGHT: green; LED-0603
LINE_SENSE_1, LINE_SENSE_2: QRE1113
LOGO1: OSHW_LOGO_FILLX0100-NT; OSHW_FILLX100_NOTEXT
M1, M2: STEPPER_MOTOR_SMD
MEM: MEM_24AA025UID; SOT23-6-MCP1640
MOTOR_CTRL_L: LB1836M; LSOP-14
MOTOR_CTRL_R: LB1836M; LSOP-14
R1, R3: 1k; 0603
R2, R6, R8, R10, R11: 10k; 0603
R4, R9: 0.1; 1206
R5, R7: 100; 0603
SMD_PAD_LEFT: PIN_SMD2.5X1.0; PIN_SMD_2.5X1.0
SMD_PAD_RIGHT: PIN_SMD2.5X1.0; PIN_SMD_2.5X1.0
TEMP_LEFT: STLM20_TEMP; UDFN4
TEMP_RIGHT: STLM20_TEMP; UDFN4
TP1, TP2, TP3, TP4, TP5, TP6, TP7, TP8, TP9, TP10, TP11, TP12, TP13, TP14, TP15, TP16, TP17, TP18, TP19, TP20, TP21, TP22, TP23, TP24, TP25, TP26, TP27, TP28: PTR1B1,27; B1,27

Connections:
A4_SDA: ATMEGA328P.27 (PC4(ADC4/SDA)), JP_I2C.2, MEM.3 (SDA), TP10.TP
A5_SCL: ATMEGA328P.28 (PC5(ADC5/SCL)), JP_I2C.1, MEM.1 (SCL), TP9.TP
AD2_LINE_LEFT: ATMEGA328P.25 (PC2(ADC2)), LINE_SENSE_2.1 (A), R6.1, TP27.TP
AD3_LINE_RIGHT: ATMEGA328P.26 (PC3(ADC3)), LINE_SENSE_1.1 (A), R8.1, TP8.TP
CURRENT_LEFT: ATMEGA328P.23 (PC0(ADC0)), CUR_LEFT.3 (IOUT), R10.2, TP19.TP
CURRENT_RIGHT: ATMEGA328P.24 (PC1(ADC1)), CUR_RIGHT.3 (IOUT), R11.2, TP18.TP
ESP_RESET: ATMEGA328P.1 (PD3(INT1)), JP_RST.2, TP1.TP
GND: ATMEGA328P.3 (GND), ATMEGA328P.5 (AGND), ATMEGA328P.21 (GND), C1.2, C2.2, C3.2, C4.1, C9.2, JP_CHRG_L.1, JP_GND.1, JP_GND.2, JP_POWER.3, JP_PROG.5, JP_VCHRG.1, LINE_SENSE_1.2 (K), LINE_SENSE_1.4 (E), LINE_SENSE_2.2 (K), LINE_SENSE_2.4 (E), MEM.2 (VSS), MEM.4 (A1), MEM.5 (A0), MOTOR_CTRL_L.7 (GND), MOTOR_CTRL_L.14 (GND1), MOTOR_CTRL_R.7 (GND), MOTOR_CTRL_R.14 (GND1), R1.1, R3.1, R10.1, R11.1, TEMP_LEFT.3 (GND), TEMP_RIGHT.3 (GND), TP2.TP
LED_LEFT: ATMEGA328P.32 (PD2(INT0)), LED_LEFT.A, TP26.TP
LED_RIGHT: ATMEGA328P.2 (PD4(XCK/T0)), LED_RIGHT.A, TP13.TP
LINE_LEFT: ATMEGA328P.30 (PD0(RXD)), R5.2, TP28.TP
LINE_RIGHT: ATMEGA328P.31 (PD1(TXD)), R7.2, TP11.TP
M1IN1: ATMEGA328P.13 (PB1(OC1A)), MOTOR_CTRL_L.2 (IN1), TP23.TP
M1IN2: ATMEGA328P.14 (PB2(SS/OC1B)), MOTOR_CTRL_L.6 (IN2), TP24.TP
M1IN3: ATMEGA328P.12 (PB0(ICP)), MOTOR_CTRL_L.13 (IN3), TP22.TP
M1IN4: ATMEGA328P.11 (PD7(AIN1)), MOTOR_CTRL_L.9 (IN4), TP21.TP
M1OUT1: M1.2, MOTOR_CTRL_L.3 (OUT1)
M1OUT2: M1.1, MOTOR_CTRL_L.5 (OUT2)
M1OUT3: M1.4, MOTOR_CTRL_L.12 (OUT3)
M1OUT4: M1.3, MOTOR_CTRL_L.10 (OUT4)
M2IN1: ATMEGA328P.9 (PD5(T1)), MOTOR_CTRL_R.2 (IN1), TP16.TP
M2IN2: ATMEGA328P.10 (PD6(AIN0)), MOTOR_CTRL_R.6 (IN2), TP17.TP
M2IN3: ATMEGA328P.8 (PB7(XTAL2/TOSC2)), MOTOR_CTRL_R.13 (IN3), TP15.TP
M2IN4: ATMEGA328P.7 (PB6(XTAL1/TOSC1)), MOTOR_CTRL_R.9 (IN4), TP14.TP
M2OUT1: M2.2, MOTOR_CTRL_R.3 (OUT1)
M2OUT2: M2.1, MOTOR_CTRL_R.5 (OUT2)
M2OUT3: M2.4, MOTOR_CTRL_R.12 (OUT3)
M2OUT4: M2.3, MOTOR_CTRL_R.10 (OUT4)
MISO: ATMEGA328P.16 (PB4(MISO)), JP_PROG.4, TP6.TP
MOSI: ATMEGA328P.15 (PB3(MOSI/OC2)), JP_PROG.2, TP7.TP
unnamed: LED_LEFT.C, R3.2
unnamed: LINE_SENSE_2.3 (C), R5.1
unnamed: LINE_SENSE_1.3 (C), R7.1
unnamed: LED_RIGHT.C, R1.2
RESET: ATMEGA328P.29 (PC6(/RESET)), JP_PROG.1, JP_RST.1, R2.1, TP5.TP
SCK: ATMEGA328P.17 (PB5(SCK)), JP_PROG.6, TP4.TP
TEMP_LEFT: ATMEGA328P.22 (ADC7), TEMP_LEFT.1 (VOUT), TP25.TP
TEMP_RIGHT: ATMEGA328P.19 (ADC6), TEMP_RIGHT.1 (VOUT), TP12.TP
VCC: ATMEGA328P.4 (VCC), ATMEGA328P.6 (VCC), ATMEGA328P.18 (AVCC), ATMEGA328P.20 (AREF), C2.1, C3.1, C4.2, JP_POWER.1, JP_PROG.3, MEM.6 (VCC), MOTOR_CTRL_L.1 (VCC), MOTOR_CTRL_R.1 (VCC), R2.2, R6.2, R8.2, TEMP_LEFT.4 (VCC), TEMP_RIGHT.4 (VCC), TP3.TP
VCHRG: JP_CHRG_R.1, JP_VCHRG.2, TP20.TP
VDD: CUR_LEFT.2 (VSENSE+), CUR_RIGHT.2 (VSENSE+), JP_POWER.2, R4.2, R9.2
VMOTOR_L: C1.1, CUR_LEFT.1 (VSENSE-), MOTOR_CTRL_L.4 (VS1), MOTOR_CTRL_L.11 (VS2), R4.1
VMOTOR_R: C9.1, CUR_RIGHT.1 (VSENSE-), MOTOR_CTRL_R.4 (VS1), MOTOR_CTRL_R.11 (VS2), R9.1

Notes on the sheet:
Connectors
Microcontroller Atmega Atmega168P
Visual output LED
Motor Controllers LB1836M
Stepper Motors
IR Line Sensors Fairchild QRE1113
ESP8266 RESET
Fiducials
Daniel Pickem
Charge Connectors
Input pins for Charging Circuit
Temperature Sensors
Current Sensors
EEPROM with unique ID
Testpoints (for programming)
Test points

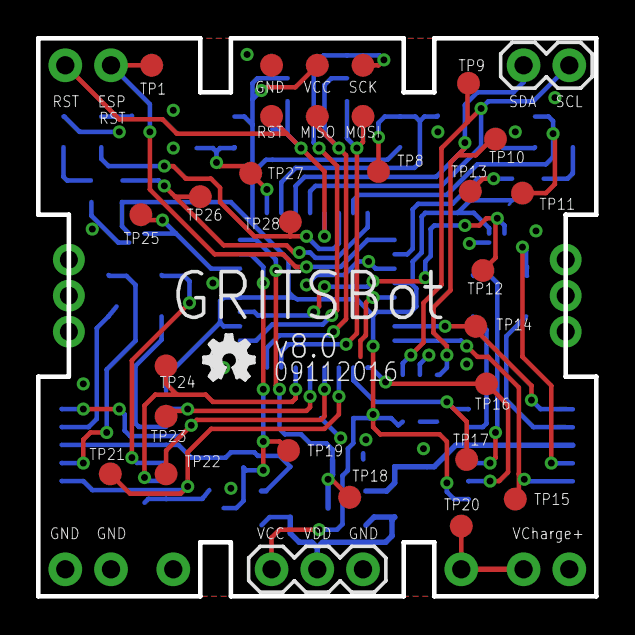
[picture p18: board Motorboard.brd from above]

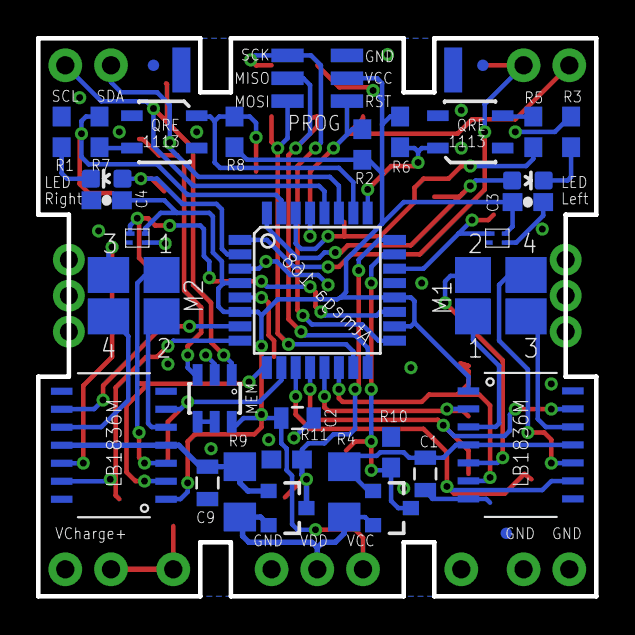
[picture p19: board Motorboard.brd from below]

Board: 2 copper layers, 31.0 x 31.0 mm, 75 parts (36 on the bottom side), 43 nets.

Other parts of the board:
FRAME3: FRAME-LETTER; CREATIVE_COMMONS

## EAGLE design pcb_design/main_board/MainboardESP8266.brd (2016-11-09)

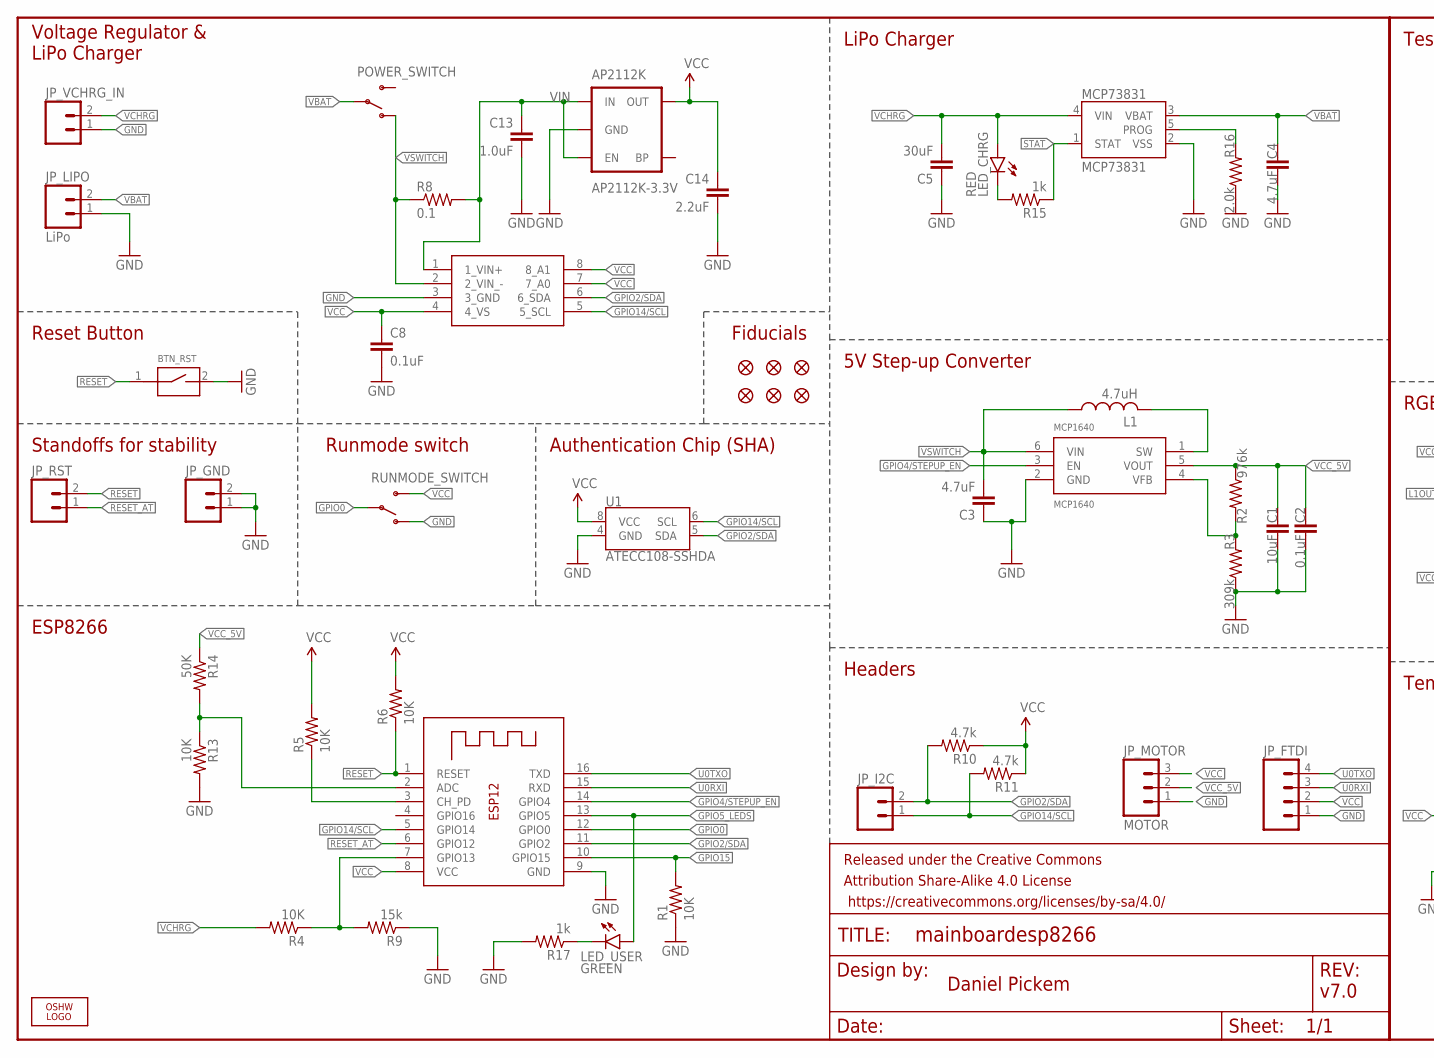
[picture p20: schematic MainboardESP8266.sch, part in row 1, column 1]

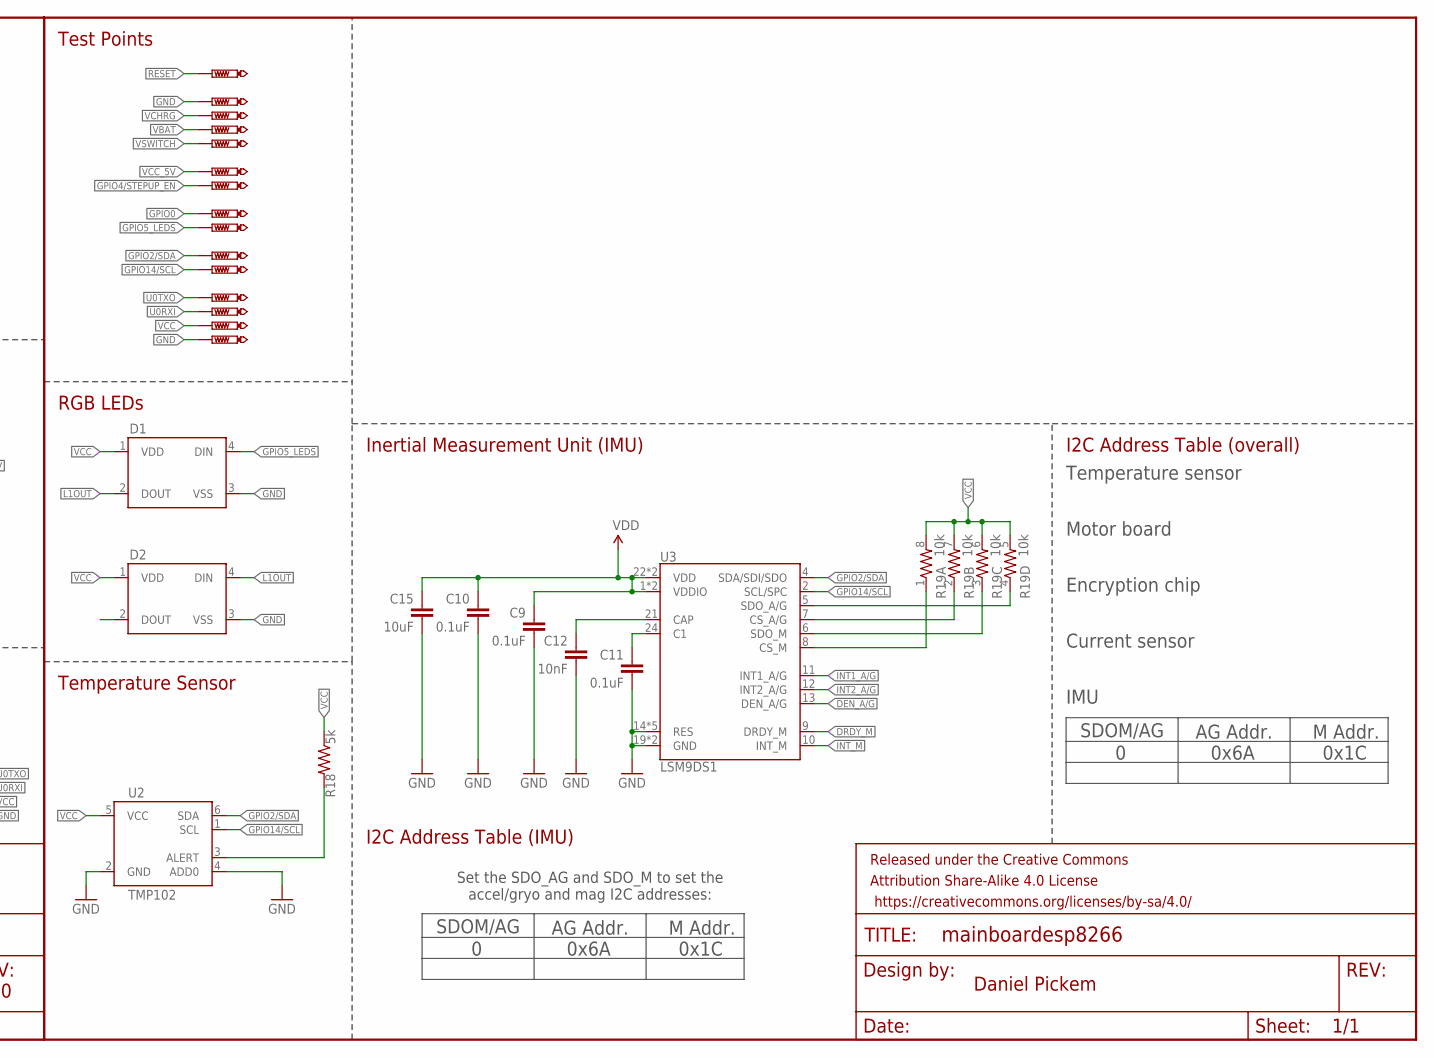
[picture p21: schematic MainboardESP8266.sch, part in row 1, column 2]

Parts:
AP2112K: AP2112K-3.3V; SOT23-5
BTN_RST: BUTTON_TACTILE_SLIM
C1: 10uF; 0603-CAP@1
C2, C8: 0.1uF; 0603-CAP@1
C3, C4: 4.7uF; 0603-CAP@1
C5: 30uF; 1206
C9, C10, C11: 0.1uF; 0603-CAP
C12: 10nF; 0603-CAP
C13: 1.0uF; 0805
C14: 2.2uF; 0603-CAP@1
C15: 10uF; 0603-CAP
D1, D2: WS2812B
ESP8266: ESP-12; ESP-12-07
FRAME1, FRAME2: FRAME-LETTER; CREATIVE_COMMONS
INA219: INA219; SOT-23-8
JP1, JP2, JP3, JP4, JP5, JP6: FIDUCIAL1X2.5; FIDUCIAL-1X2.5
JP_FTDI: M041X04_NO_SILK; 1X04_NO_SILK
JP_GND: M021X02_NO_SILK; 1X02_NO_SILK
JP_I2C: M02PTH; 1X02
JP_LIPO: LiPo; 1X02
JP_MOTOR: MOTOR; 1X03
JP_RST: M021X02_NO_SILK; 1X02_NO_SILK
JP_VCHRG_IN: M021X02_NO_SILK; 1X02_NO_SILK
L1: 4.7uH; INDUCTOR_NR3015
LED_CHRG: RED; LED-0603
LED_USER: GREEN; LED-0603
LOGO1: OSHW_LOGO_FILLX0100-NT; OSHW_FILLX100_NOTEXT
MCP1640: MCP1640; SOT23-6-MCP1640
MCP73831: MCP73831; SOT23-5
POWER_SWITCH: SWITCH-SPDT-SMD-A; SWITCH-SPST-SMD-A
R1, R4, R5, R6, R13: 10K; 0603-RES@1
R2: 976k; 0603-RES@1
R3: 309k; 0603-RES@1
R8: 0.1; 1206
R9: 15k; 0603-RES@1
R10, R11: 4.7k; 0603
R14: 50K; 0603-RES@1
R15, R17: 1k; 0603-RES@1
R16: 2.0k; 0603-RES@1
R18: 5k; 0603-RES@1
R19: 10k; 0603-ARV
RUNMODE_SWITCH: SWITCH-SPDT-SMD-A; SWITCH-SPST-SMD-A
TP1, TP2, TP3, TP4, TP5, TP6, TP7, TP8, TP9, TP10, TP11, TP12, TP13, TP14, TP15: PTR1B1,27; B1,27
U1: ATECC108-SSHDA; SO08
U2: TMP102; SOT563
U3: LSM9DS1; LGA24-8X4

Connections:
ADC: ESP8266.2 (ADC), R13.1, R14.2
C1: C11.1, U3.24 (C1)
CAP: C12.1, U3.21 (CAP)
CHIP_EN1: ESP8266.3 (CH_PD), R5.1
CS_A/G: R19.2 (1), U3.7 (CS_A/G)
CS_M: R19.1, U3.8 (CS_M)
DEN_A/G: U3.13 (DEN_A/G)
DRDY_M: U3.9 (DRDY_M)
GND: AP2112K.2 (GND), BTN_RST.2, C1.2, C2.2, C3.1, C4.2, C5.1, C8.2, C9.2, C10.2, C11.2, C12.2, C13.2, C14.2, C15.2, D1.3 (VSS), D2.3 (VSS), ESP8266.9 (GND), INA219.3 (3_GND), JP_FTDI.1, JP_GND.1, JP_GND.2, JP_LIPO.1, JP_MOTOR.1, JP_VCHRG_IN.1, MCP1640.2 (GND), MCP73831.2 (VSS), R1.1, R3.1, R9.1, R13.2, R16.1, R17.2, RUNMODE_SWITCH.1 (O), TP5.TP, TP8.TP, U1.4 (GND), U2.2 (GND), U2.4 (ADD0), U3.14 (RES), U3.15 (RES), U3.16 (RES), U3.17 (RES), U3.18 (RES), U3.19 (GND), U3.20 (GND)
GPIO0: ESP8266.12 (GPIO0), RUNMODE_SWITCH.2, TP14.TP
GPIO2/SDA: ESP8266.11 (GPIO2), INA219.6 (6_SDA), JP_I2C.2, R10.2, TP6.TP, U1.5 (SDA), U2.6 (SDA), U3.4 (SDA/SDI/SDO)
GPIO4/STEPUP_EN: ESP8266.14 (GPIO4), MCP1640.3 (EN), TP12.TP
GPIO5_LEDS: D1.4 (DIN), ESP8266.13 (GPIO5), LED_USER.A, TP15.TP
GPIO14/SCL: ESP8266.5 (GPIO14), INA219.5 (5_SCL), JP_I2C.1, R11.2, TP7.TP, U1.6 (SCL), U2.1 (SCL), U3.2 (SCL/SPC)
GPIO15: ESP8266.10 (GPIO15), R1.2
INT1_A/G: U3.11 (INT1_A/G)
INT2_A/G: U3.12 (INT2_A/G)
INT_M: U3.10 (INT_M)
L1OUT: D1.2 (DOUT), D2.4 (DIN)
L2OUT: D2.2 (DOUT)
unnamed: LED_CHRG.C, R15.2
unnamed: MCP73831.5 (PROG), R16.2
unnamed: MCP1640.4 (VFB), R2.2, R3.2
unnamed: ESP8266.7 (GPIO13), R4.1, R9.2
unnamed: R18.2, U2.3 (ALERT)
unnamed: L1.P$2 (2), MCP1640.1 (SW)
unnamed: LED_USER.C, R17.1
RESET: BTN_RST.1, ESP8266.1 (RESET), JP_RST.2, R6.1, TP1.TP
RESET_AT: ESP8266.6 (GPIO12), JP_RST.1
SDO_A/G: R19.4 (1), U3.5 (SDO_A/G)
SDO_M: R19.3 (1), U3.6 (SDO_M)
STAT: MCP73831.1 (STAT), R15.1
U0RXI: ESP8266.15 (RXD), JP_FTDI.3, TP3.TP
U0TXO: ESP8266.16 (TXD), JP_FTDI.4, TP2.TP
VBAT: C4.1, JP_LIPO.2, MCP73831.3 (VBAT), POWER_SWITCH.2, TP9.TP
VCC: AP2112K.5 (OUT), C8.1, C9.1, C10.1, C14.1, C15.1, D1.1 (VDD), D2.1 (VDD), ESP8266.8 (VCC), INA219.4 (4_VS), INA219.7 (7_A0), INA219.8 (8_A1), JP_FTDI.2, JP_MOTOR.3, R5.2, R6.2, R10.1, R11.1, R18.1, R19.5 (2), R19.6 (2), R19.7 (2), R19.8 (2), RUNMODE_SWITCH.3 (S), TP4.TP, U1.8 (VCC), U2.5 (VCC), U3.1 (VDDIO), U3.3 (VDDIO), U3.22 (VDD), U3.23 (VDD)
VCC_5V: C1.1, C2.1, JP_MOTOR.2, MCP1640.5 (VOUT), R2.1, R14.1, TP13.TP
VCHRG: C5.2, JP_VCHRG_IN.2, LED_CHRG.A, MCP73831.4 (VIN), R4.2, TP11.TP
VIN: AP2112K.1 (IN), AP2112K.3 (EN), C13.1, INA219.1 (1_VIN+), R8.2
VSWITCH: C3.2, INA219.2 (2_VIN_-), L1.P$1 (1), MCP1640.6 (VIN), POWER_SWITCH.1 (O), R8.1, TP10.TP

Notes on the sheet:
Daniel Pickem
Voltage Regulator & LiPo Charger
ESP8266
Headers
v7.0
5V Step-up Converter
Authentication Chip (SHA)
Standoffs for stability
Runmode switch
Fiducials
Reset Button
LiPo Charger
Test Points
RGB LEDs
Temperature Sensor
Set the SDO_AG and SDO_M to set the accel/gryo and mag I2C addresses:
I2C Address Table (IMU)
Inertial Measurement Unit (IMU)
I2C Address Table (overall)
SDOM/AG
0x1C
AG Addr.
M Addr.
0x6A
IMU
Current sensor
Temperature sensor
Motor board
Encryption chip



Board: 2 copper layers, 31.0 x 31.0 mm, 77 parts (49 on the bottom side), 34 nets.

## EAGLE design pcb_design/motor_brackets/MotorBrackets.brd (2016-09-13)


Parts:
FRAME1: FRAME-LETTER; CREATIVE_COMMONS
JP1, JP2, JP3, JP5: M01PTH; 1X01

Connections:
GND1: JP1.1, JP3.1
GND2: JP2.1, JP5.1

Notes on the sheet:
Daniel Pickem
SMD Pads for Motor Stands

Board: 2 copper layers, 5 parts (0 on the bottom side), 2 nets, no tracks yet.

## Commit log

2016-09-13 Added schematic and PCB design for the GRITSBot main board
    [MainboardESP8266.brd, MainboardESP8266.sch]
2016-09-13 Added schematic and PCB design for the GRITSBot motor board
    [Motorboard.brd, Motorboard.sch]
2016-09-13 Added motor brackets for the GRITSBot's motor board
    These motor brackets are made out of PCB material like the main
    and motor board of the robot. Each bracket is glued to the motor
    board and functions as caster pins so that the robot is statically
    stable. Note that these motor brackets can be replaced with the
    3D printed part that also functions as charging coil mount (see
    folder '3d_model' in this repository.
    [MotorBrackets.brd, MotorBrackets.sch]
2016-09-13 Added 3D model of the robot
    [Frame.ipt, Frame.stp]
2016-09-13 Added prototype of GRITSBot shell
    [Shell.stp]
2016-09-13 Added charging coil mount
    [Charging_frame_base.stp, Charging_frame_cap.stp]
2016-09-13 Added 3D model of robot including its shell
    [Main.ipt, Main.stp]
2016-09-13 Added bill of materials for GRITSBot
    The bill of materials (BoM) includes the BoM for the main board,
    the motor board, as well as additional components needed to
    assemble the robot.
    [bom.xlsx]
2016-09-15 Added images of the latest main and motor board prototypes
2016-10-19 Updated the GRITSBot's motor board
    1. Added a reset pin so that the main board can reset
    the motor board.
    2. Fixed the polarity of the current sensors.
    3. Added test pins on the top layer.
    4. Added castellated edges to mount motors mechanically
    more stable.
    [Motorboard.brd, Motorboard.sch]
2016-10-25 Moved test points to allow for pogo pins on test board
    [Motorboard.brd, Motorboard.sch]
2016-10-25 Removed reverse polarity protection on charge input
    [Motorboard.brd, Motorboard.sch]
2016-10-25 Added IMU and temperature sensor to main board
    [MainboardESP8266.brd, MainboardESP8266.sch]
2016-11-02 Fixed RGB LED setup on main board.
    The RGB LEDs were connected to GPIO16, which on some versions
    of the ESP8266 is connected to the RESET pin and can't be used
    as general purpose pin after all. The RGB LEDs are now connected
    to GPIO5 - the same pin as the status LED. Both types of LEDs can
    be used together on the same pin.
    [MainboardESP8266.brd, MainboardESP8266.sch, Motorboard.brd]
2016-11-09 Merged Main Board Test pin location changes into master
    [MainboardESP8266.brd]
2016-11-09 Added test pin for GPIO5
    [MainboardESP8266.brd, MainboardESP8266.sch]
2016-11-09 Changed LED color value on motor board
    [Motorboard.brd, Motorboard.sch]
2016-11-09 Added BoM for main and motor board
    [bom.csv]
2016-11-14 Minor silk screen changes to mMotor board
    [Motorboard.brd, Motorboard.sch]
2016-11-14 Minor comment change on motor board schematic
    [Motorboard.sch]
2016-12-05 TestBoard Designs
    [Test_MainboardESP8266.brd, Test_MainboardESP8266.sch, Test_Motorboard.brd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]
2016-12-05 Added TODO comments on test board designs
    [Test_MainboardESP8266.brd, Test_Motorboard.brd, Test_Motorboard.sch]

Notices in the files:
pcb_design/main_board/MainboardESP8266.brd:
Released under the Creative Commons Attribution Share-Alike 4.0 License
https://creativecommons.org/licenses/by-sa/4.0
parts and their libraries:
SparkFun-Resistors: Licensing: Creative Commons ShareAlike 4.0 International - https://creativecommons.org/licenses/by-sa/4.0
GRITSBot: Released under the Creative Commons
